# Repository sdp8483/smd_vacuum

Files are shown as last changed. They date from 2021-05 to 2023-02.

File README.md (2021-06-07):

# Manual Pick and Place SMD Vacuum

*Copy from blog post: https://samueldperry.com/2021/06/07/manual-pick-and-place-smd-vacuum/*

Until recently I used tweezers when populating surface mount parts on a PCB. Browsing around on YouTube late one night I stumbled upon a video by [SDG Electronics](https://www.youtube.com/channel/UCMiC9bSMux7i2Ds6sIqDaFg) about making a [Manual Pick and Place SMD Vacuum](https://www.youtube.com/watch?v=9G510G2gmdo&t=24s). There is also a [part 2](https://www.youtube.com/watch?v=1FnGqH_WkL4&list=RDCMUCMiC9bSMux7i2Ds6sIqDaFg&index=3) for those interested. I was then motivated to make up my own since it looked so much easier then using tweezers. There was no parts list from SDG Electronics that I could find so I set about searching for suitable components and designing my own simple controller PCB. Below is a description of the mechanical and electrical designing of the SMD Vacuum that I ended up building.

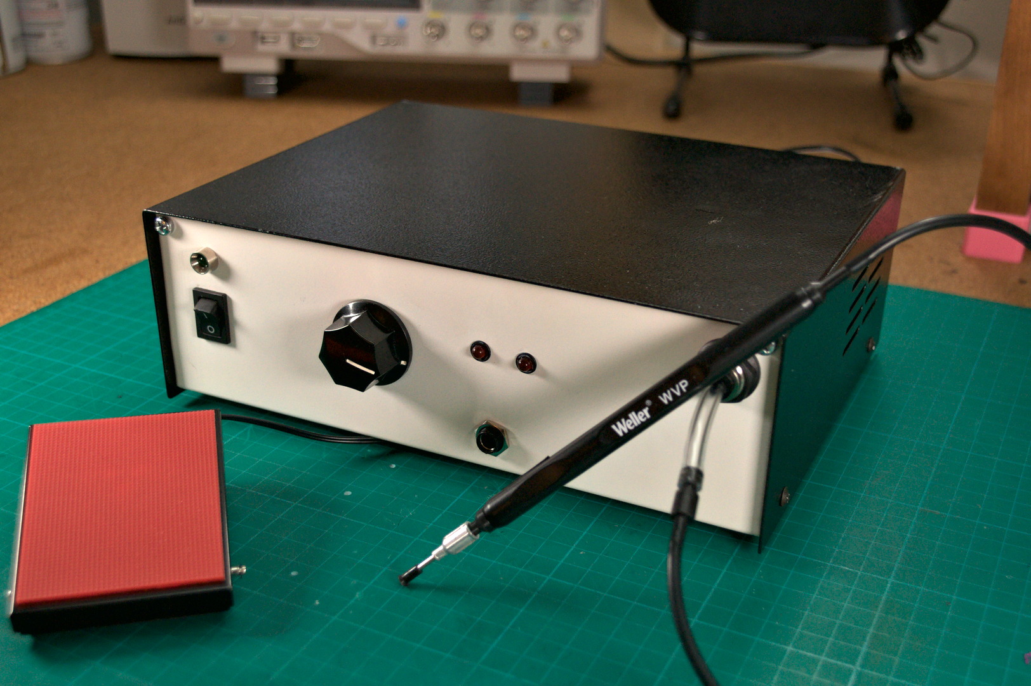
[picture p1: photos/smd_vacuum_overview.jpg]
SMD Vacuum


## Bill Of Materials

Below is a bill of materials with supplier links of all the major mechanical and electrical components. The PCB controller components are presented in a separate BOM below without suggested supplier links since all the components are generic and can be sourced from the usual suspects.
No. |Item|	Qty.|	Suggested Supplier Link
-----|----|-----|--------------------------|
1|	Metal Enclosure, 7.5″ x 9.8″ x 3.2″|	1|	[Jameco](https://www.jameco.com/webapp/wcs/stores/servlet/ProductDisplay?productId=209358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)
2|	LED Panel Mounting Hardware|	10|	[Jameco](https://www.jameco.com/webapp/wcs/stores/servlet/ProductDisplay?productId=23077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)
3|	12V Diaphragm Vacuum Pump|	1|	[eBay](https://www.ebay.com/itm/221615572829?epid=1545518177&hash=item339951475d:g:GFgAAOSwhMFZqyRF)**
4|	12V Pneumatic Shutoff Valve|	1|	[eBay](https://www.ebay.com/itm/114832826636?hash=item1abc91e10c:g:bG0AAOSwbg9gtVNb)
5|	1/4″ NPT Inline Filter/Snubber|	1|	[eBay](https://www.ebay.com/itm/132229655610)
6|	Vacuum Pick & Place Tool|	1|	[DigiKey](https://www.digikey.com/en/products/detail/apex-tool-group/T0052918499N/1801476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)
7|	1/4″ PVC Tubing|	50ft|	[McMaster-Carr](https://www.mcmaster.com/5233K52/)
8|	1/4″ Tube Fitting, Through Wall|	1|	[McMaster-Carr](https://www.mcmaster.com/5779K272/)
9|	1/4″ Tube Fitting to 1/4″ NPT Male|	3|	[McMaster-Carr](https://www.mcmaster.com/7880T125/)
10|	12V 1.3A AC to DC Power Supply|	1|	[Jameco](https://www.jameco.com/webapp/wcs/stores/servlet/ProductDisplay?productId=1919051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)
11|	1/4″ Phone Jack|	2|	[Jameco](https://www.jameco.com/webapp/wcs/stores/servlet/ProductDisplay?productId=297537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)
12|	IEC 320-C14 Power Entry Module with Fuse|	1|	[Amazon](https://www.amazon.com/Module-Socket-Connector-Blades-Holder/dp/B07TQMW2D9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)*
13|	Rocker Switch|	1|	[Amazon](https://www.amazon.com/QTEATAK-Rocker-Switch-Position-Terminals/dp/B08B84H8WL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)*
14|	3mm LED, Red/Green|	3|	[Amazon](https://www.amazon.com/Chanzon-100pcs-colors-Emitting-Assorted/dp/B01AUI4W5U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)*
15|	100k Potentiometer with Knob|	1|	[Amazon](https://www.amazon.com/TWTADE-rv24yn20s-Variable-Potentiometer-Regulation/dp/B07DHFYLRV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)*
16|	Foot Switch with 1/4″ Plug|	1|	[eBay](https://www.ebay.com/itm/272420357567)
17|	Various Fasteners and Similar Hardware|		
18|	Assembled Controller|	1|	See BOM Below

*I didn’t buy these exact items since I had them already from previous projects but these should be equivalent to what I used. Substitutions are possible for items you have on hand.

**When I was looking for a small vacuum pump eBay was flooded with the Parker 12V Dual Head Vacuum Pump which is what I got. But now it seems to be out of stock and since it looks like it was a surplus item it is probably out of stock for good. The linked vacuum pump looks like it will work just as well but I have not tested it.

No.|	Item|	Qty.
---|--------|-------
1|	PCB|	1
2|	10nF Ceramic Capacitor|	1
3|	100uF 25V Electrolytic Capacitor|	2
4|	1N4148 Diode|	2
5|	1N4007 Diode|	2
6|	IRF5305 P-channel MOSFET|	1
7|	N-channel MOSFET|	2
8|	4.7k 1/4W Through Hole Resistor|	1
9|	1k 1/4W Through Hole Resistor|	7
10|	NE555P 555 Timer|	1
11|	817 Optocoupler|	1
12|	8 pin DIP IC Socket|	1
13|	2 Position Screw Terminal|	5
14|	JST Socket with Matching Connectors and Pins|	2

## Controller PCB

Yes this project uses a 555 timer, as a electronics hobbyist I am contractually obligated to use it in at least one project. While the solution by SDG Electronics with a microcontroller is perfectly valid and what I would have normally used, I decided to finally use a 555 timer in a project. I hate the 555 timer and find it completely unnecessary in today’s microcontroller dominated world. Why use a IC that requires external components when a few lines of code and less components will produce the same result with more accurate timings? I have to admit that at the end of this project I had a little respect for the 555 timer and found it a good challenge to try to manipulate it to do what I wanted. I may briefly consider it in future simple projects.

The PCB is designed to enable milling on a CNC router such as the 3018 Pro and that is what I did. [Gerbers](https://github.com/sdp8483/smd_vacuum/tree/main/pcb/gerber) are available but be warned I did not pay any attention to the silkscreen so some component labels could be in strange spots or missing. If you want to get your PCBs made I would suggest opening the KiCAD design files and fixing the silkscreen labels before.

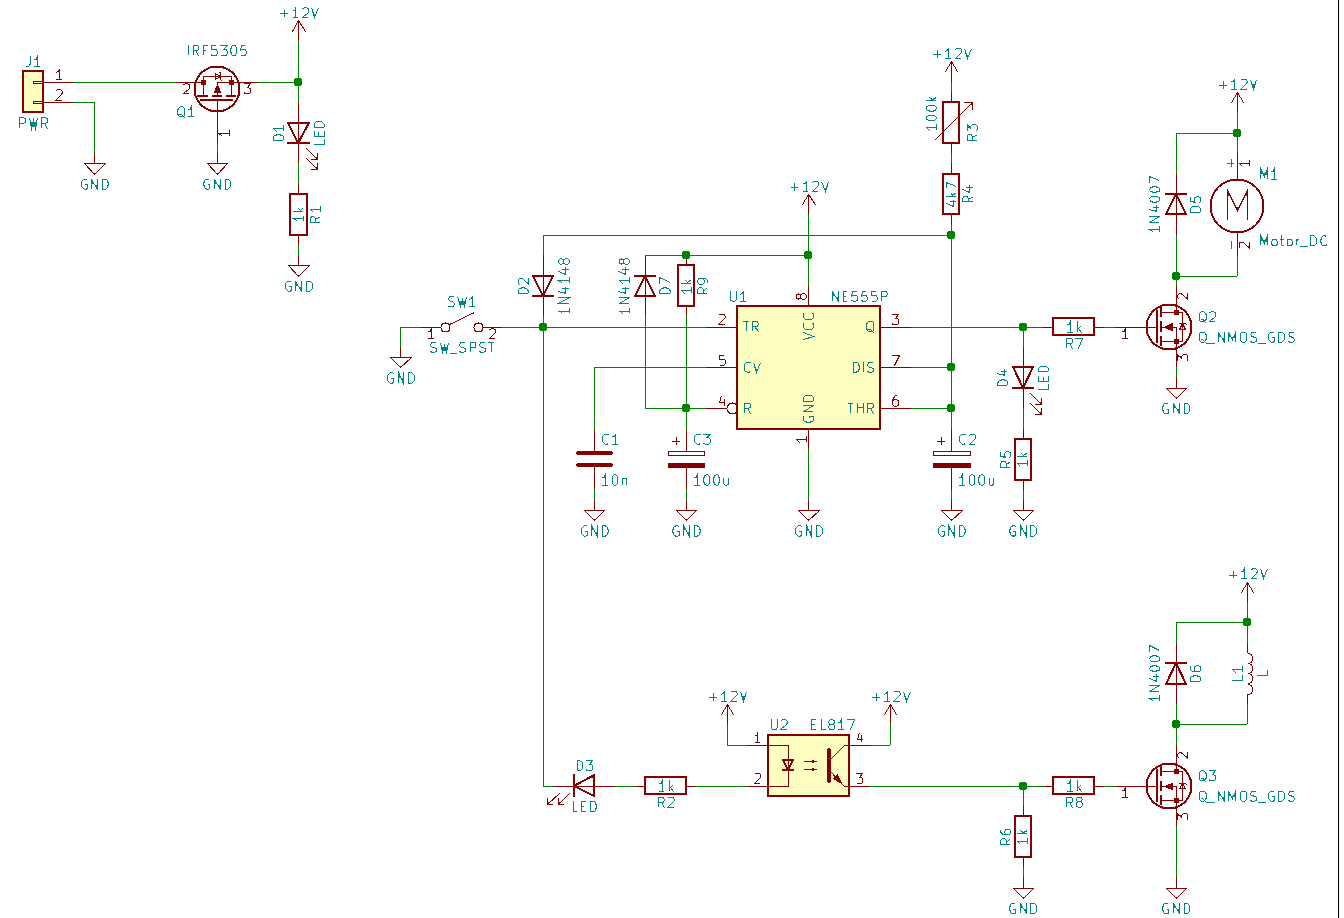
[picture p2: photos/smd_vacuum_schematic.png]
schmatic


The circuit is fairly simple, closing SW1 (the foot switch) turns on the vacuum pump and opens the shutoff valve. LED D2 and D3 will be illuminated. Releasing SW1 will close the shutoff valve turning off suction upstream of the shutoff valve and LED D3 will turn off. The vacuum pump will continue to run based on the position of the 100k potentiometer, somewhere between 1 and 15 seconds.

PCB assembly is easy when following the [interactive bom](https://github.com/sdp8483/smd_vacuum/tree/main/pcb/bom). In the pictures you may notice mine has a bodge since my first design neglected the reset on power circuitry and I had to add that after I noticed that sometimes on first power up the controller would turn on the vacuum pump. The PCB design has been updated with those components so no need for you to bodge them in.

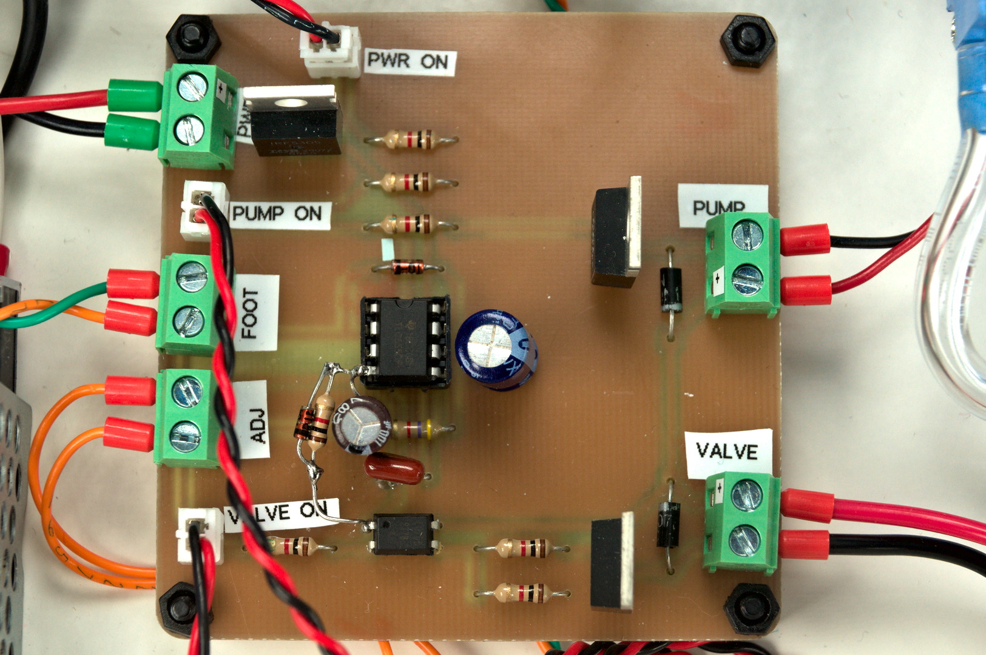
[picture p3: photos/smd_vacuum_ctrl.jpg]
PCB


## Assembly

I will go over briefly how I assembled my SMD Vacuum but will omit many details since you most likely will not be using the same vacuum pump and you may wish your layout to be slightly different.

First thing I did was to arrange all the components inside the enclosure so that I could see if everything would fit. I roughly knew that I wanted to keep the power supply and its AC wiring on the left of the case, with the controller in the middle and the pneumatics on the right side of the case. I also arranged the front and back panels to look like I wanted. Pencil works great since it can easily be cleaned off later.

I started with mounting the AC power input socket, rocker switch, and 12V power supply. I wired the rocker switch to cut power to the input of the 12V power supply so that when the unit is turned off there will be zero current draw. Don’t forget to attach the earth ground from the AC socket to the case using a bolt and star washer. Sand off some of the paint under the washer on the case to make a good metal to metal connection. Also attach the earth ground of the 12V power supply to this same point. This way the case is grounded and is safer.

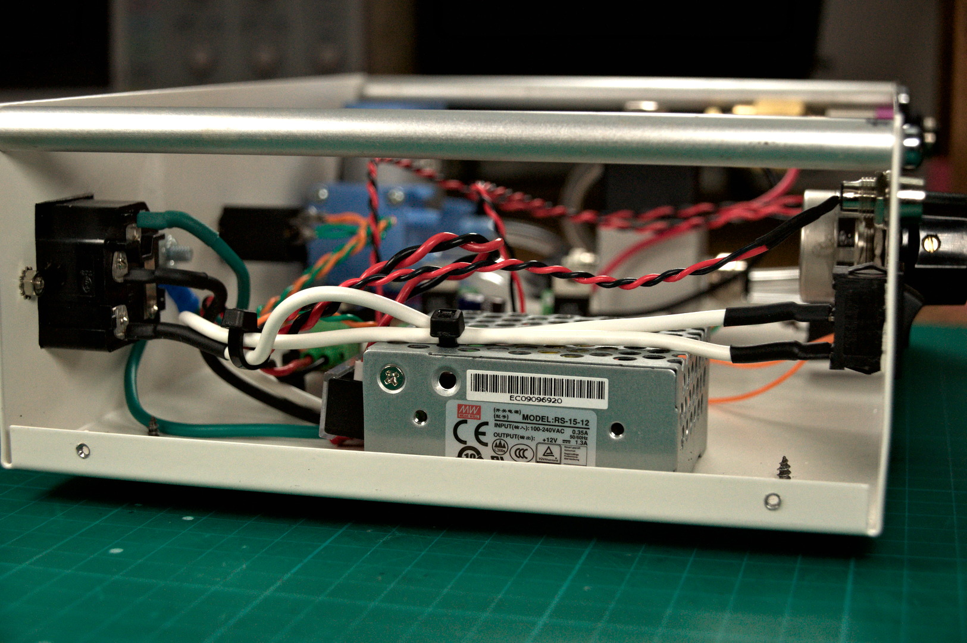
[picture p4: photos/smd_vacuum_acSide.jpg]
AC Power Side

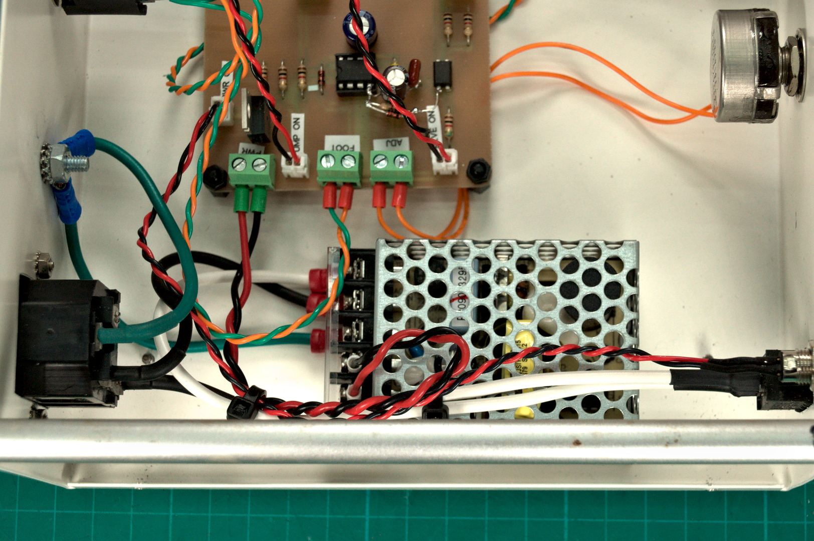
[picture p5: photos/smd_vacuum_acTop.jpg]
AC Power Top

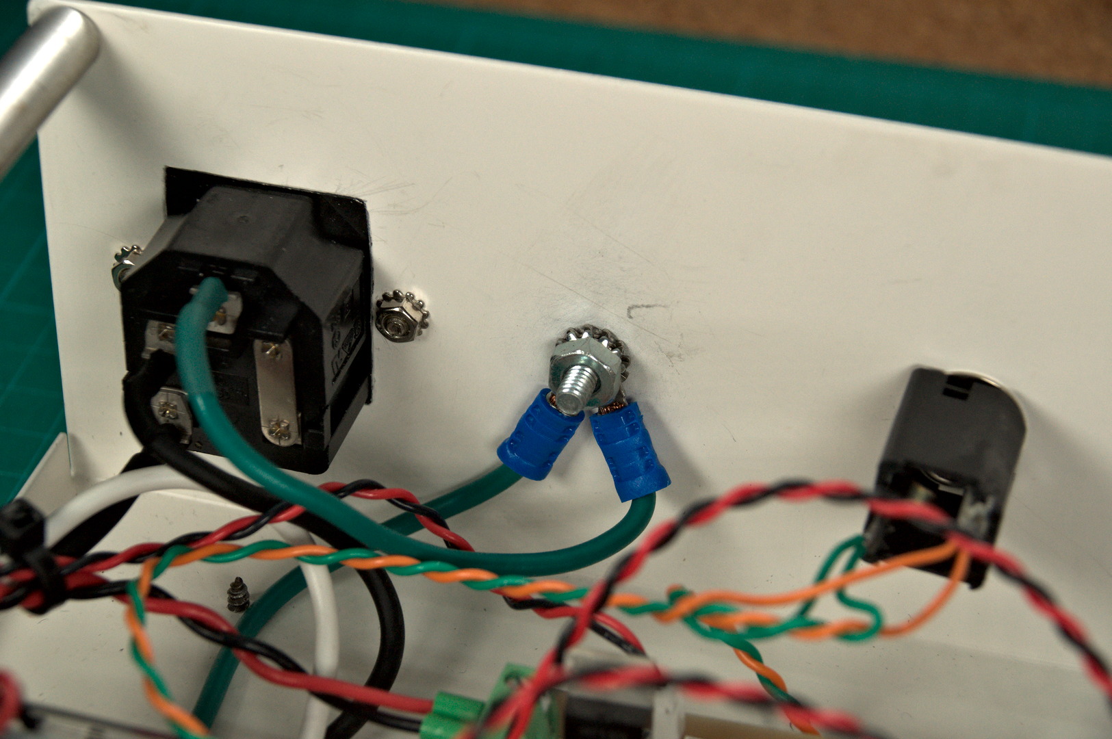
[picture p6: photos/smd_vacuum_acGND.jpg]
AC Power GND


I then mounted the controller PCB using nylon standoffs near the center of the case and oriented it so that the power input terminal is close to the 12V power supply. At the same time I mounted the 100k potentiometer, LEDs, and 1/4″ jacks. I used two 1/4″ jacks in parallel because I wanted both the front and back panels to have a jack. This way I can plug the foot switch into whatever panel is most convenient for wire management.

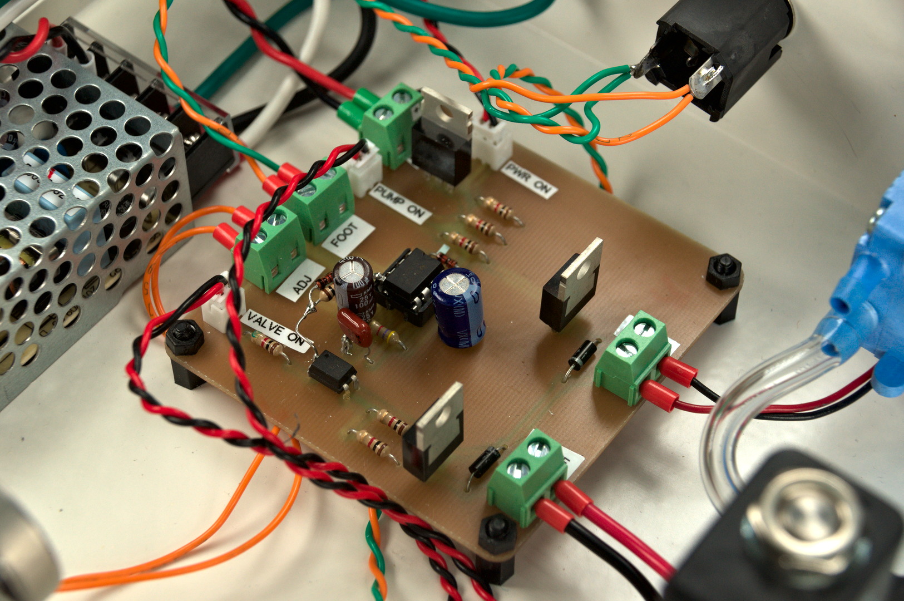
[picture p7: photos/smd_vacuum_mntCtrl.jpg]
Controler Mount

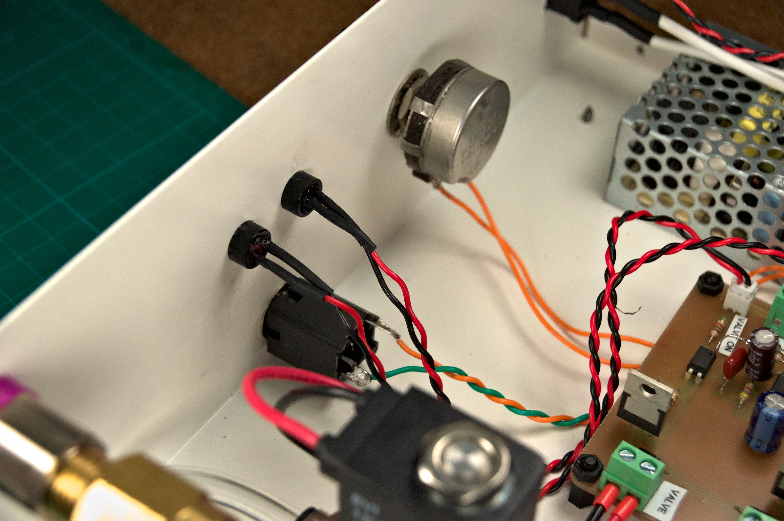
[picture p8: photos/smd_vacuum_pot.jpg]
Pot and LEDs


For the pnumatics I 3D printed some standoffs so that they would not be resting directly on the case. This was mostly done because of the length of fasteners I had and also to dampen the noise produced by the vacuum pump. I plumbed the punmatics as shown below with the shutoff valve between the pump and the filter followed by the panel mounted 1/4″ tube fitting. The filter is absolutely necessary as I have already sucked up quite a few 0603 parts and having the filter saves the shutoff valve and pump from damage.

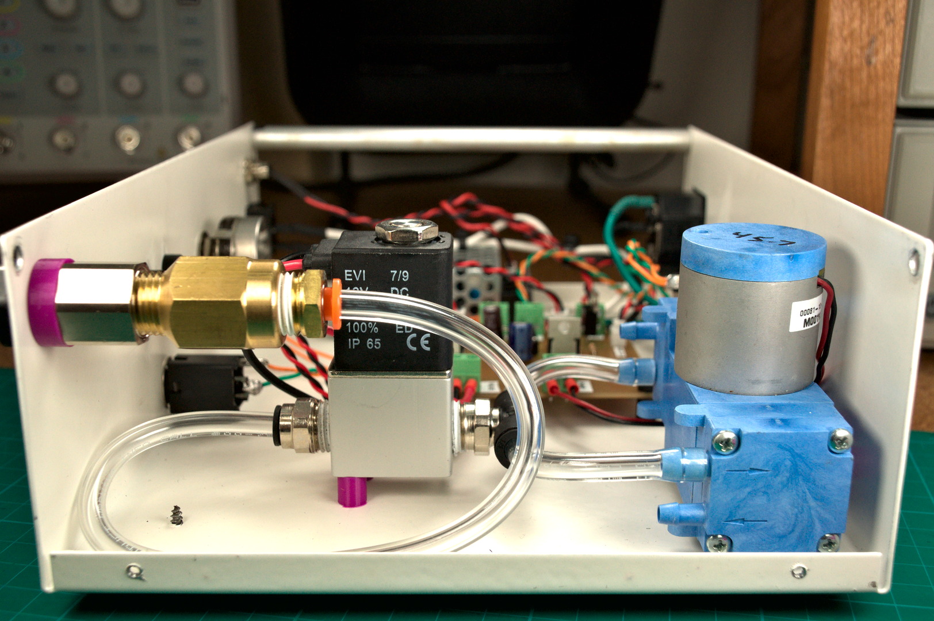
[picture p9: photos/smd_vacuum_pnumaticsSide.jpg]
pnumatics side

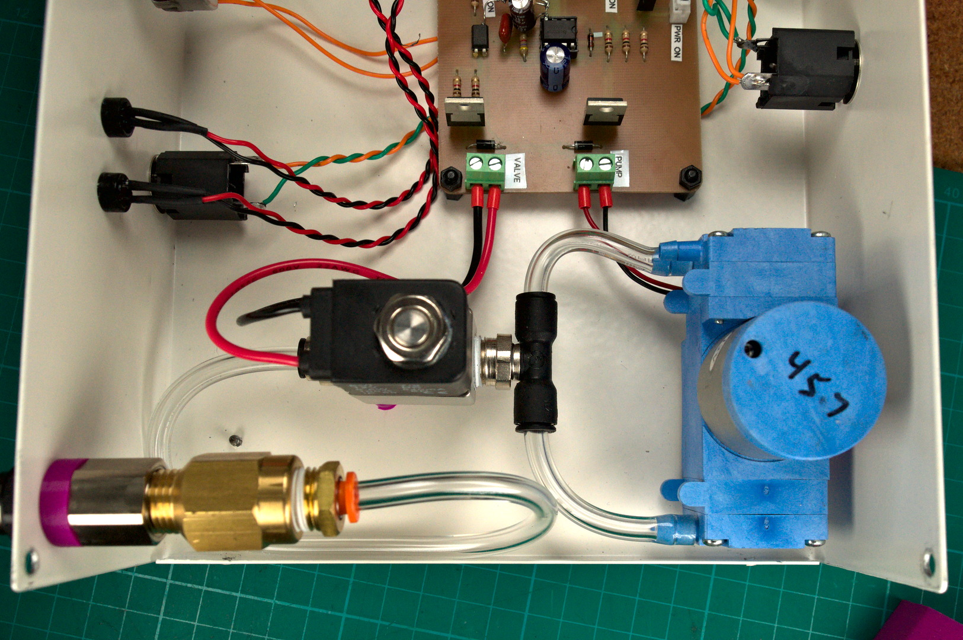
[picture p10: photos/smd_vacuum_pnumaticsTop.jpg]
pnumatics top


That was about all the steps I took for assembly, fairly simple. The aluminum bars in the pictures were added to increase the stiffness of the front and back panel when plugging in connectors and tubing.

## Hand piece

Aside from the vacuum pump the second most important item for this build is the hand piece. This is the part that you hold and use to pickup SMD parts. I was able to find a used Weller WVP on eBay. I would suggest looking there or other used market places first since it is relatively expensive brand new for some reason. The part number to search for is T0052918499N or look for replacement parts for a Weller WR3M Station. [DigiKey](https://github.com/sdp8483/smd_vacuum/tree/main/pcb/bom) sells a new Weller WVP for $88. The Weller WVP is adapted to the SMD Vacuum by cutting a small section of the 1/4″ PVC tubing and inserting the plastic nozzle on the end hand piece into the tubing as shown below. Finally block the hole on the side of the Weller WVP since we are using to foot pedal to control suction and not your finger.

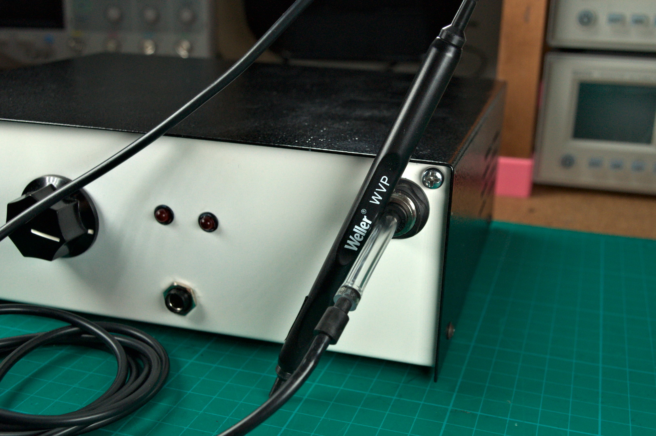
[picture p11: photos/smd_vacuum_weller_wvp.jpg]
Weller WVP


This hand piece feels really nice and works well for me. Having said that if you cannot find one for a decent price or feel like making your own hand piece I did do a little experimentation and found that it is possible to make something similar while not as well polished. I used a [1/8″ OD Brass Tube](https://www.mcmaster.com/8859K19/) and connected it to the front port of the SMD Vacuum using [1/4″ OD Soft Tygon PVC Tubing](https://www.mcmaster.com/5552k23/). The clear PVC tubing used inside the SMD Vacuum is a little stiff for my liking and I found that Tygon tubing is slightly more pliant. The photos below show the rough setup I was experimenting with before I found the Weller Hand Piece. My plan was to 3D print a case to go around the brass tube for gripping and to also 3D print adapters so that the nozzles could connect better to the brass tube. As pictured it works fine although not very ergonomic. For nozzles I used a rubber protective cover that comes on the engraving bits for the 3018 pro with a small hole that I drilled in the end. This setup was a rough prototype that I would have refined more had I not picked up a Weller WVP.

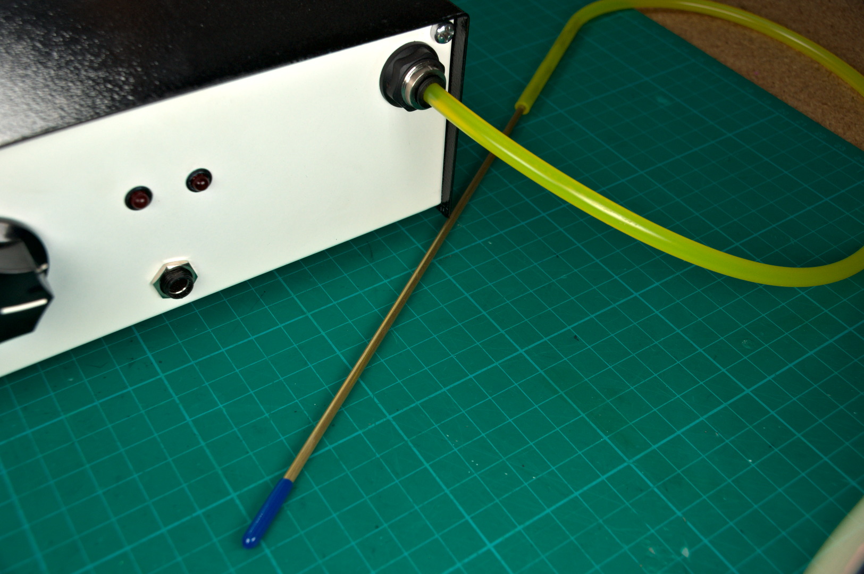
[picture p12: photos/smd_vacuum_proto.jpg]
proto hand piece


## Nozzles

Nozzles, you will need some. The Weller WVP comes with some nozzles and suction cup tips. You can also get these nozzle and cups with one of the cheap [vacuum suction pens](https://www.amazon.com/Jiayouy-Precision-Component-Placement-Interchangeable/dp/B08SWG12G3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). These nozzles and suction cups are great for picking up larger SMD packages like microcontrollers and power MOSFETs but they are not useful for small packages such as 0603 resistors and capacitors. The suction cup gets in the way and grips the part so well that it will not release when suction is turned off. Removing the suction cup is not possible since the nozzle ID is large enough that a 0603 resistor can get sucked up it. Remember that filter, this is why it is installed before the shutoff valve.

What I found that works great for these small packages is [blunt tip needles for syringes](https://www.amazon.com/dp/B07RSTQ6RV?psc=1&ref=ppx_yo2_dt_b_product_details). I got a variety pack with 14ga, 16ga,18ga, 20ga, 22ga and 25ga needles along with some syringes. I found the 20ga needle (pink) to be the perfect size for picking up 0603 packages along with SOT-23 transistors and some larger packages. The part drops off as soon a suction is off and you can see the part while manipulating it. The only problem is that the nozzle requires you to work with the hand piece vertical since it does not have the angle on it like the nozzles that came with the Weller WVP. If I get adventurous I may try bending one someday but for now I found working vertical gave me better position control.

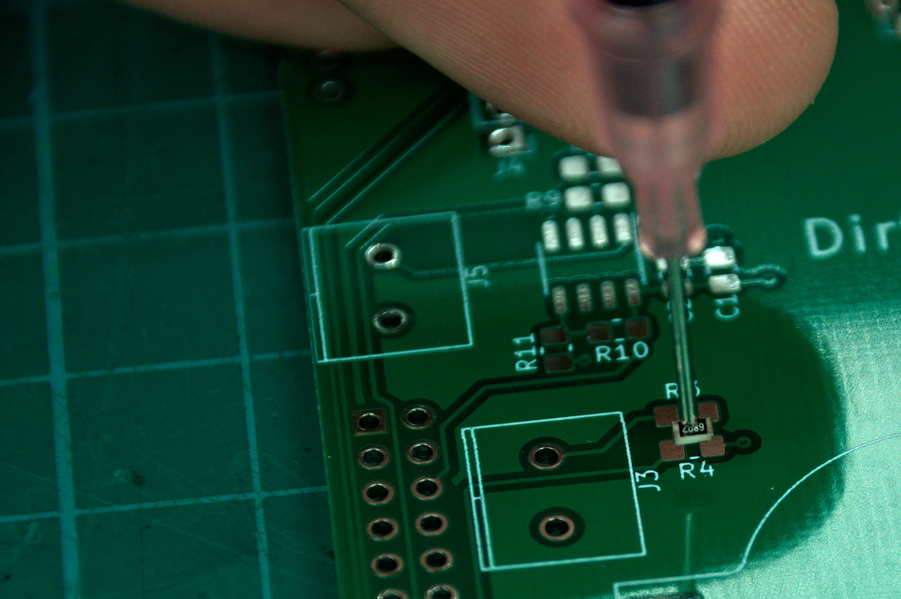
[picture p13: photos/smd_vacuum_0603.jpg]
nozzle in use 1

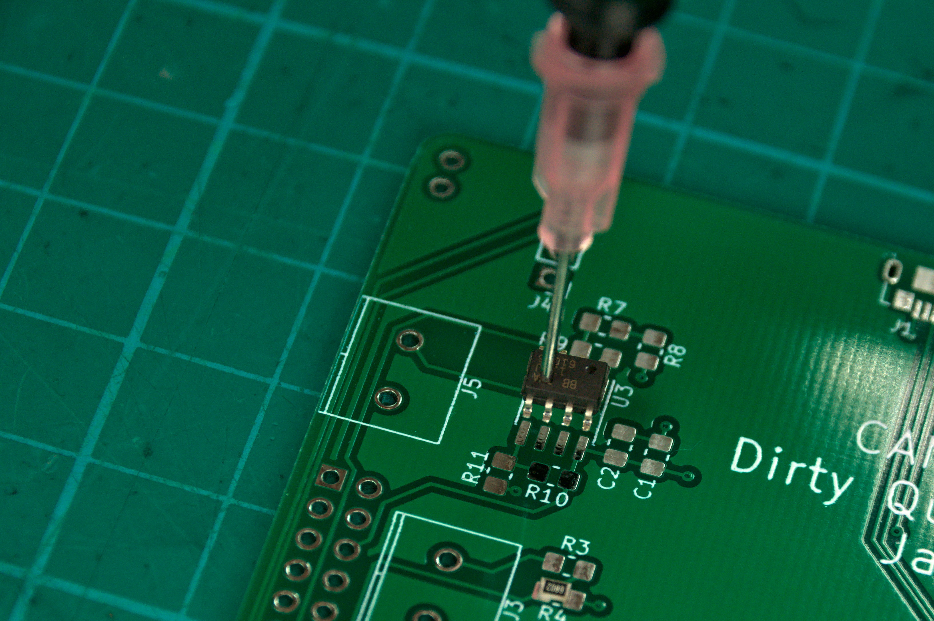
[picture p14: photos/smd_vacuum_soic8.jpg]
nozzle in use 2


## Conclusion

That wraps up this project. I am very happy with how it turned out and its function. I successfully assembled a small run of 10 PCBs with 64 components per board using this SMD Vacuum without any issues. Utilizing the blunt needle tip along with one of the suction cup tips that came with the Weller WVP I was able to handle all the SMD parts for those PCBs. The smallest package size was 0603 and the largest package was a ESP-12F WiFi module. The SMD Vacuum had enough suction power to lift everything and made placement easy. Goodby tweezers, hello SMD Vacuum.

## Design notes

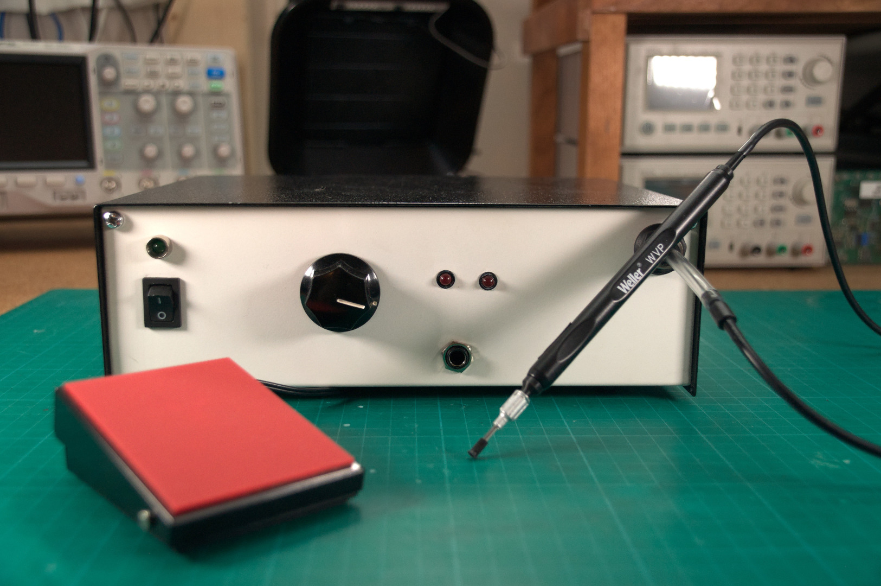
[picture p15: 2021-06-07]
photos/smd_vacuum_cover.jpg

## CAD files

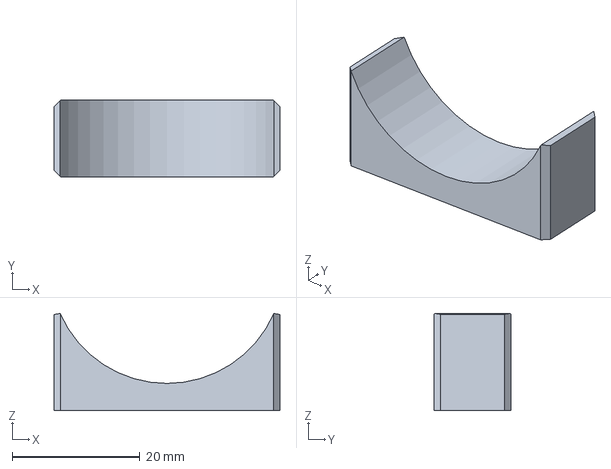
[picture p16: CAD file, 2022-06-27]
enclosure/KarlssonRobotics_pump_mount-base.amf
35.4 x 12.0 x 15.2 mm

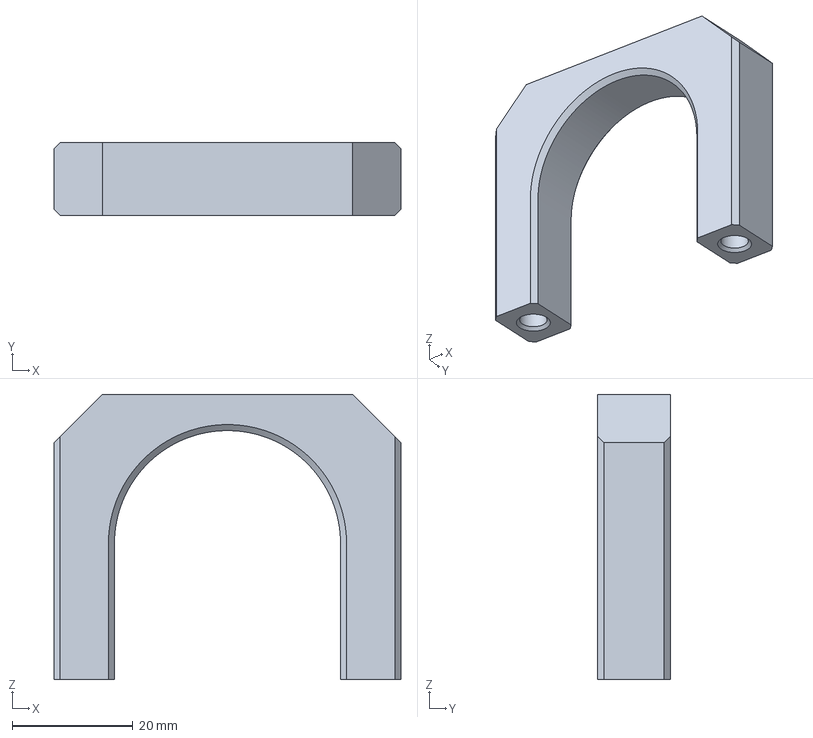
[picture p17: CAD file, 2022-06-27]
enclosure/KarlssonRobotics_pump_mount-clamp.amf
57.4 x 12.0 x 47.2 mm

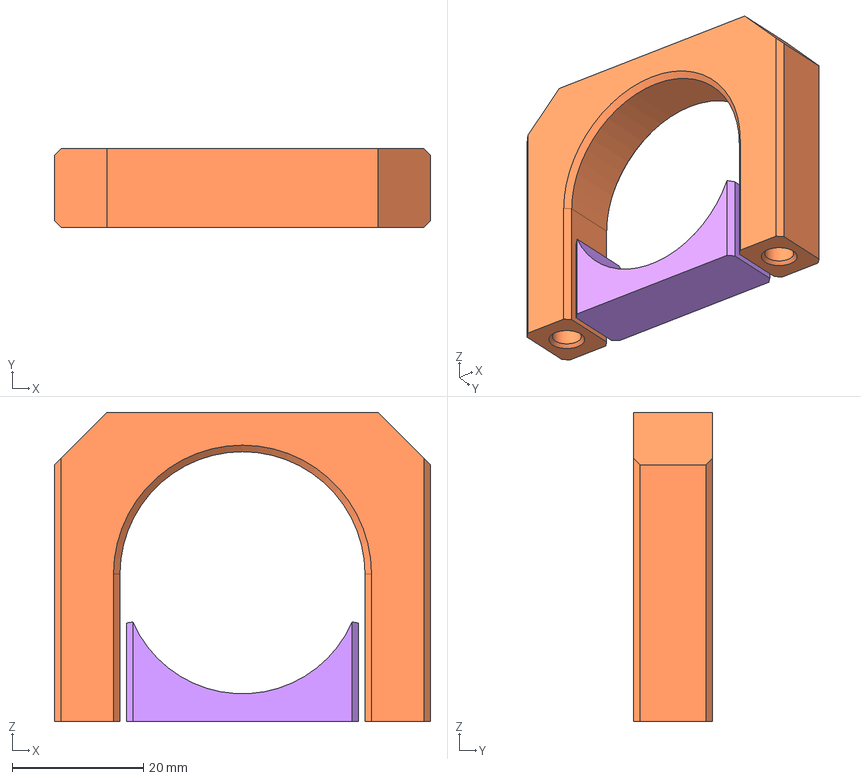
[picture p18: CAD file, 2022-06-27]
enclosure/KarlssonRobotics_pump_mount.FCStd
57.4 x 12.0 x 47.2 mm
clamp
base

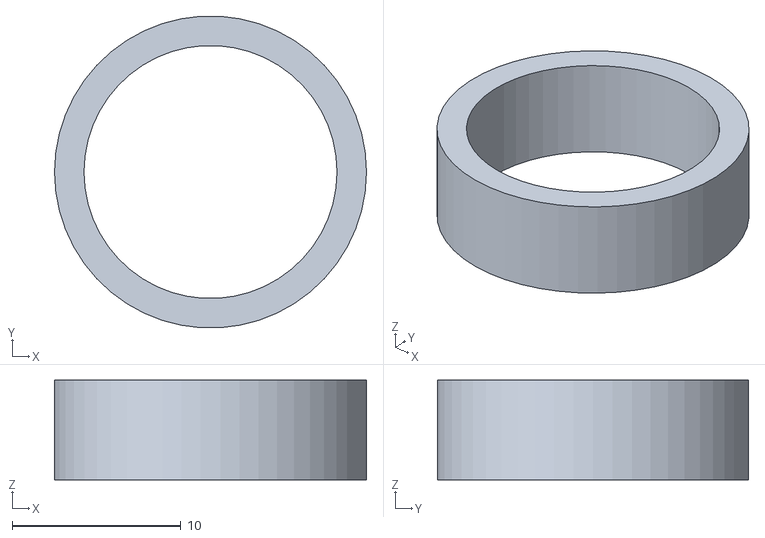
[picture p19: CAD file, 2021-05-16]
enclosure/air_spacer.stl
18.5 x 18.5 x 5.90

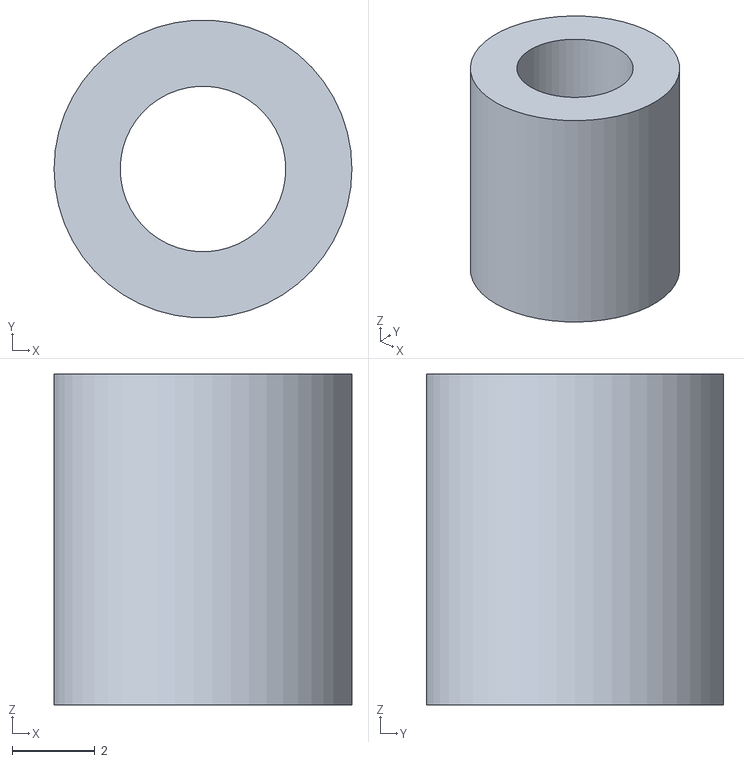
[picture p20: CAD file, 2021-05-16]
enclosure/valve_spacer.stl
7.20 x 7.19 x 8.00

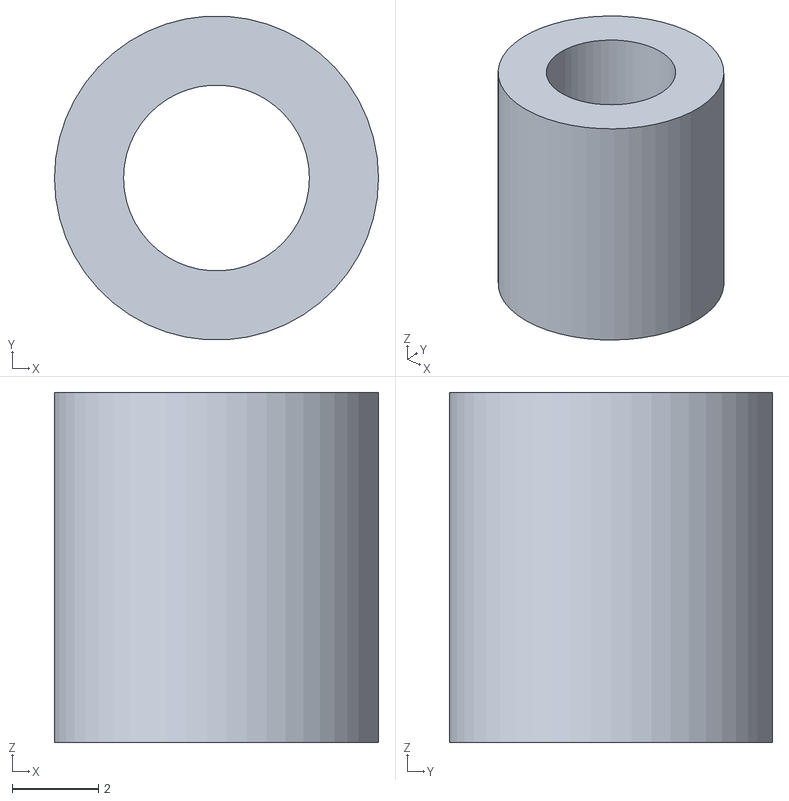
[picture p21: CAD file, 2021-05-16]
enclosure/pump_spacer.stl
7.50 x 7.49 x 8.10

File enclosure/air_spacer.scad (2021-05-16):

$fn = 50;

L = 5.9;
id = 15;
od = 18.5;

difference() {
    cylinder(h=L, d=od);
    cylinder(h=L, d=id);
}

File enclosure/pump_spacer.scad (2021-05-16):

$fn = 50;

L = 12.3-3-1.2;
id = 4.3;
od = 2*((id/2) + (0.4*4));

difference() {
    cylinder(h=L, d=od);
    cylinder(h=L, d=id);
}

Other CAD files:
enclosure/valve_spacer.scad

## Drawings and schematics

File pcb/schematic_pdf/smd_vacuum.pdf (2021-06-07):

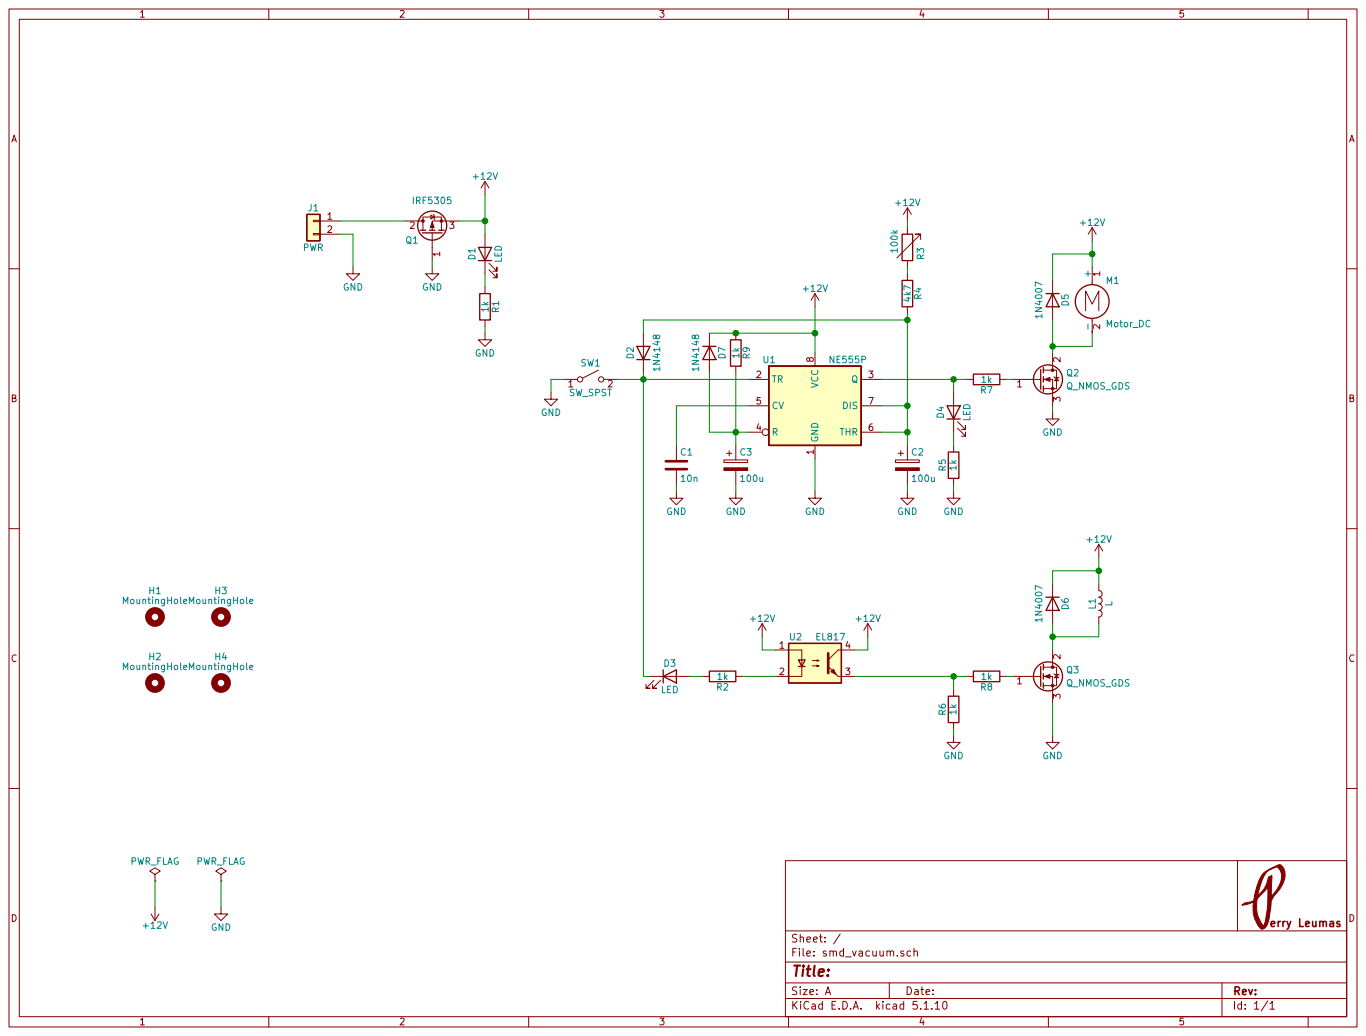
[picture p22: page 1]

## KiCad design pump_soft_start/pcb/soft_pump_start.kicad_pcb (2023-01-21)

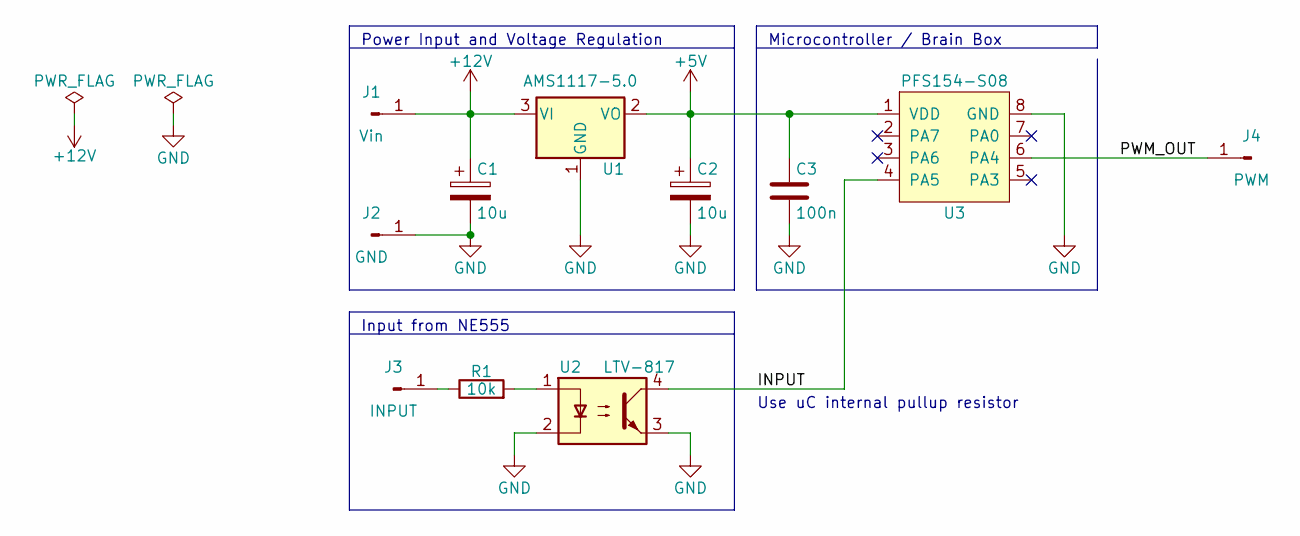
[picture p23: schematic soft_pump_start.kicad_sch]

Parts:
C1, C2: 10u; CP_Radial_D5.0mm_P2.50mm
C3: 100n; C_0603_1608Metric_Pad1.08x0.95mm_HandSolder
J1: Vin; SolderWire-0.5sqmm_1x01_D0.9mm_OD2.1mm
J2: GND; SolderWire-0.5sqmm_1x01_D0.9mm_OD2.1mm
J3: INPUT; SolderWire-0.5sqmm_1x01_D0.9mm_OD2.1mm
J4: PWM; SolderWire-0.5sqmm_1x01_D0.9mm_OD2.1mm
R1: 10k; R_0603_1608Metric_Pad0.98x0.95mm_HandSolder
U1: AMS1117-5.0; SOT-223-3_TabPin2
U2: LTV-817; DIP-4_W7.62mm
U3: PFS154-S08; SOP-8_3.9x4.9mm_P1.27mm

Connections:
+5V: C2.1, C3.1, U1.2 (VO), U3.1 (VDD)
+12V: C1.1, J1.1, U1.3 (VI)
/INPUT: U2.4, U3.4 (PA5)
/PWM_OUT: J4.1, U3.6 (PA4)
GND: C1.2, C2.2, C3.2, J2.1, U1.1 (GND), U2.2, U2.3, U3.8 (GND)
unnamed: J3.1, R1.1
unnamed: R1.2, U2.1

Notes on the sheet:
Microcontroller / Brain Box
Input from NE555
Use uC internal pullup resistor
Power Input and Voltage Regulation

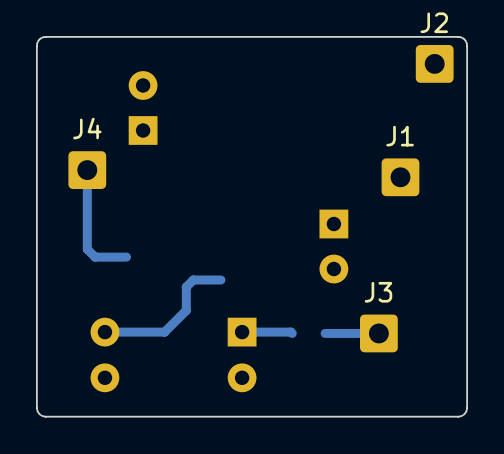
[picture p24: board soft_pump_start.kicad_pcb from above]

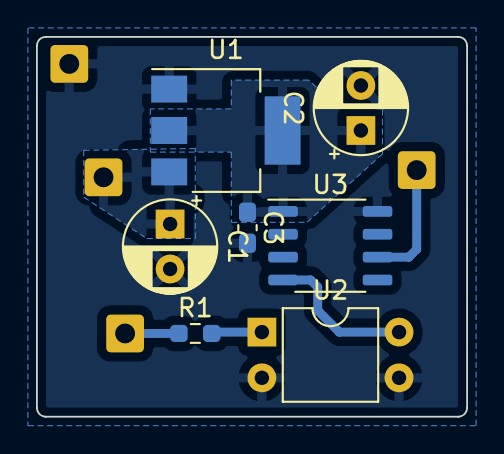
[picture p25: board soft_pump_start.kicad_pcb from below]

Board: 2 copper layers, 23.9 x 21.1 mm, 11 parts (7 on the bottom side), 7 nets.

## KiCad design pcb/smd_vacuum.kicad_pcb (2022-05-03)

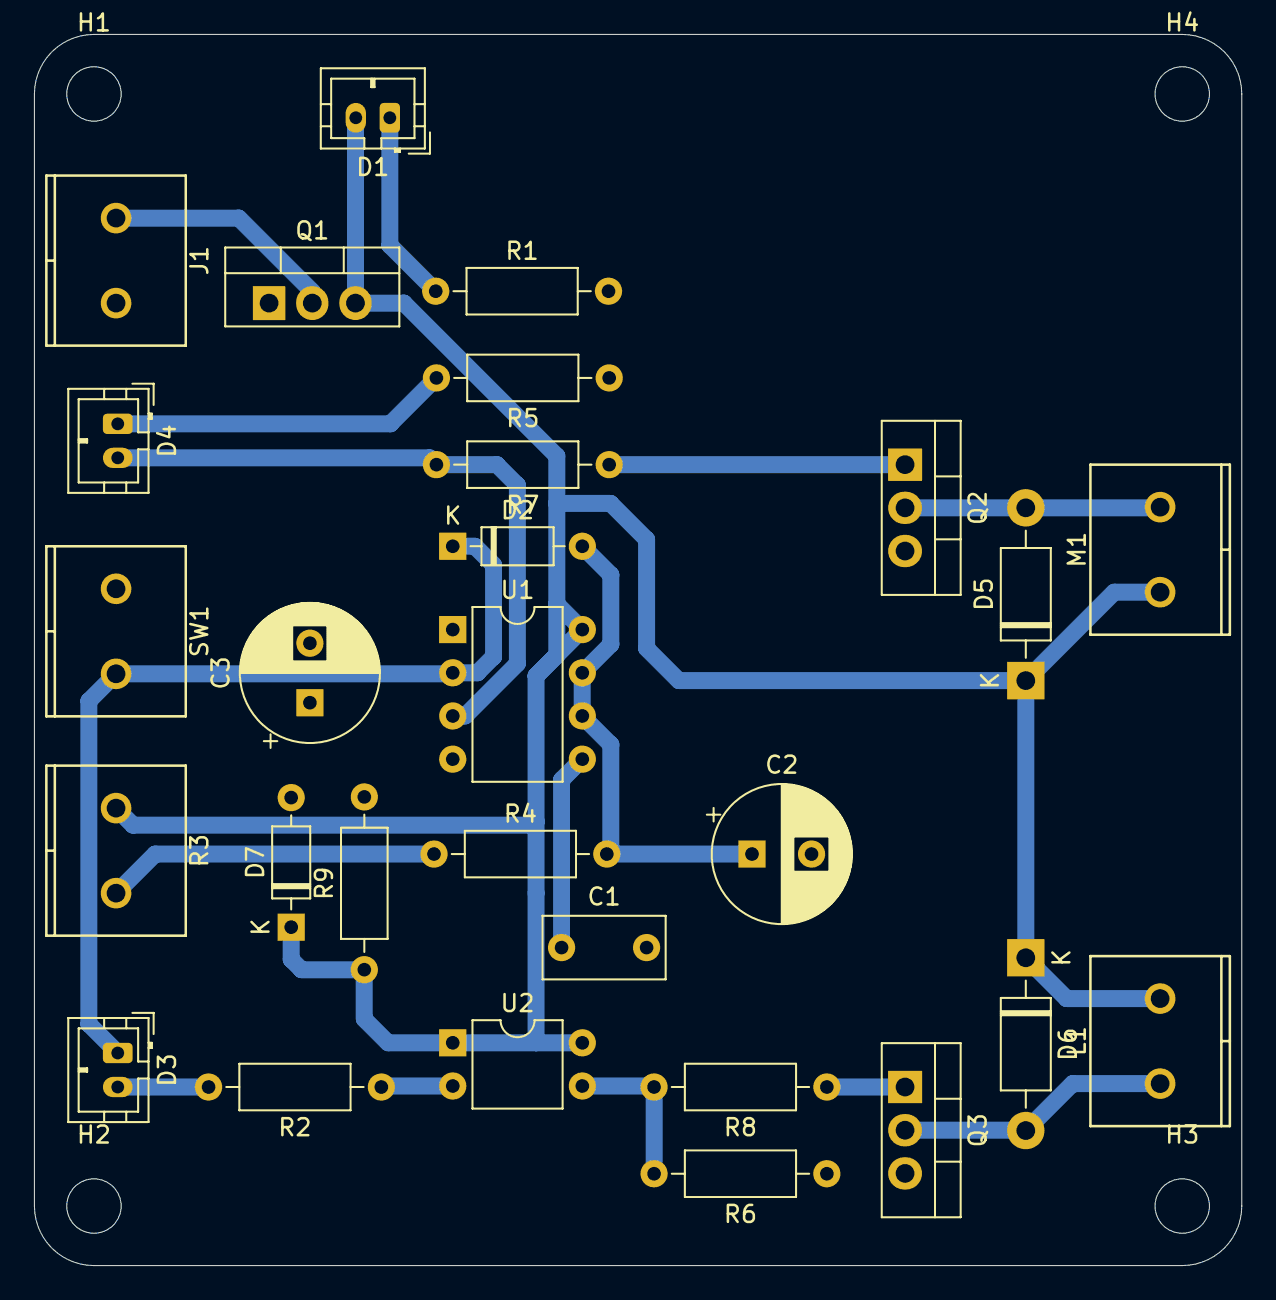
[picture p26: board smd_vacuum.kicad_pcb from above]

Board: 2 copper layers, 71.0 x 72.4 mm, 32 parts (0 on the bottom side), 18 nets.

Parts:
C1: 10n; C_Rect_L7.0mm_W3.5mm_P5.00mm
C2, C3: 100u; CP_Radial_D8.0mm_P3.50mm
D1, D3, D4: LED; JST_PH_B2B-PH-K_1x02_P2.00mm_Vertical
D2, D7: 1N4148; D_DO-35_SOD27_P7.62mm_Horizontal
D5, D6: 1N4007; D_DO-41_SOD81_P10.16mm_Horizontal
H1, H2, H3, H4: MountingHole; MountingHole_3.2mm_M3
J1: PWR; WJ127-5.0-2P
L1: L; WJ127-5.0-2P
M1: Motor_DC; WJ127-5.0-2P
Q1: IRF5305; TO-220-3_Vertical
Q2, Q3: Q_NMOS_GDS; TO-220-3_Vertical
R1, R2, R5, R6, R7, R8, R9: 1k; R_Axial_DIN0207_L6.3mm_D2.5mm_P10.16mm_Horizontal
R3: 100k; WJ127-5.0-2P
R4: 4k7; R_Axial_DIN0207_L6.3mm_D2.5mm_P10.16mm_Horizontal
SW1: SW_SPST; WJ127-5.0-2P
U1: NE555P; DIP-8_W7.62mm
U2: EL817; DIP-4_W7.62mm

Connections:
+12V: D1.2, D5.1, D6.1, D7.1, L1.2, M1.1, Q1.3, R3.1, R9.1, U1.8, U2.1, U2.4
GND: C1.2, C2.2, C3.2, J1.2, Q1.1, Q2.3, Q3.3, R1.2, R5.1, R6.1, SW1.1, U1.1
unnamed: C1.1, U1.5
unnamed: C2.1, D2.2, R4.2, U1.6, U1.7
unnamed: C3.1, D7.2, R9.2, U1.4
unnamed: D1.1, R1.1
unnamed: D2.1, D3.1, SW1.2, U1.2
unnamed: D3.2, R2.2
unnamed: D4.1, R5.2
unnamed: D4.2, R7.2, U1.3
unnamed: D5.2, M1.2, Q2.2
unnamed: D6.2, L1.1, Q3.2
unnamed: J1.1, Q1.2
unnamed: Q2.1, R7.1
unnamed: Q3.1, R8.1
unnamed: R2.1, U2.2
unnamed: R3.2, R4.1
unnamed: R6.2, R8.2, U2.3

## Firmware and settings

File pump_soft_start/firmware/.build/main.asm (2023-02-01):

;--------------------------------------------------------
; File Created by SDCC : free open source ANSI-C Compiler
; Version 4.2.0 #13081 (Linux)
;--------------------------------------------------------
	.module main
	.optsdcc -mpdk14
	

; default segment ordering in RAM for linker
	.area DATA
	.area OSEG (OVR,DATA)

;--------------------------------------------------------
; Public variables in this module
;--------------------------------------------------------
	.globl __sdcc_external_startup
	.globl _main
	.globl __delay_loop_32
	.globl __delay_loop_16
	.globl __delay_loop_8
	.globl __misclvr
	.globl __misc2
	.globl __misc
	.globl __pwmg2cubl
	.globl __pwmg2cubh
	.globl __pwmg2dtl
	.globl __pwmg2dth
	.globl __pwmg2s
	.globl __pwmg2c
	.globl __pwmg1cubl
	.globl __pwmg1cubh
	.globl __pwmg1dtl
	.globl __pwmg1dth
	.globl __pwmg1s
	.globl __pwmg1c
	.globl __pwmg0cubl
	.globl __pwmg0cubh
	.globl __pwmg0dtl
	.globl __pwmg0dth
	.globl __pwmg0s
	.globl __pwmg0c
	.globl __gpcs
	.globl __gpcc
	.globl __bgtr
	.globl __tm3b
	.globl __tm3s
	.globl __tm3ct
	.globl __tm3c
	.globl __tm2b
	.globl __tm2s
	.globl __tm2ct
	.globl __tm2c
	.globl __t16c
	.globl __t16m
	.globl __pbph
	.globl __pbc
	.globl __pb
	.globl __pbdier
	.globl __paph
	.globl __pac
	.globl __pa
	.globl __padier
	.globl __integs
	.globl __intrq
	.globl __inten
	.globl __eoscr
	.globl __ilrcr
	.globl __ihrcr
	.globl __clkmd
	.globl __sp
	.globl __flag
	.globl __delay_loop_32_PARM_1
	.globl __delay_loop_16_PARM_1
	.globl __delay_loop_8_PARM_1
;--------------------------------------------------------
; special function registers
;--------------------------------------------------------
	.area RSEG (ABS)
	.org 0x0000
__flag	=	0x0000
__sp	=	0x0002
__clkmd	=	0x0003
__ihrcr	=	0x000b
__ilrcr	=	0x0039
__eoscr	=	0x000a
__inten	=	0x0004
__intrq	=	0x0005
__integs	=	0x000c
__padier	=	0x000d
__pa	=	0x0010
__pac	=	0x0011
__paph	=	0x0012
__pbdier	=	0x000e
__pb	=	0x0014
__pbc	=	0x0015
__pbph	=	0x0016
__t16m	=	0x0006
__t16c::
	.ds 2
__tm2c	=	0x001c
__tm2ct	=	0x001d
__tm2s	=	0x0017
__tm2b	=	0x0009
__tm3c	=	0x0032
__tm3ct	=	0x0033
__tm3s	=	0x0034
__tm3b	=	0x0035
__bgtr	=	0x001a
__gpcc	=	0x0018
__gpcs	=	0x0019
__pwmg0c	=	0x0020
__pwmg0s	=	0x0021
__pwmg0dth	=	0x0022
__pwmg0dtl	=	0x0023
__pwmg0cubh	=	0x0024
__pwmg0cubl	=	0x0025
__pwmg1c	=	0x0026
__pwmg1s	=	0x0027
__pwmg1dth	=	0x0028
__pwmg1dtl	=	0x0029
__pwmg1cubh	=	0x002a
__pwmg1cubl	=	0x002b
__pwmg2c	=	0x002c
__pwmg2s	=	0x002d
__pwmg2dth	=	0x002e
__pwmg2dtl	=	0x002f
__pwmg2cubh	=	0x0030
__pwmg2cubl	=	0x0031
__misc	=	0x0008
__misc2	=	0x000f
__misclvr	=	0x001b
;--------------------------------------------------------
; ram data
;--------------------------------------------------------
	.area DATA
__delay_loop_8_PARM_1:
	.ds 1
__delay_loop_16_PARM_1:
	.ds 2
__delay_loop_32_PARM_1:
	.ds 4
_main_sloc0_1_0:
	.ds 2
;--------------------------------------------------------
; overlayable items in ram
;--------------------------------------------------------
;--------------------------------------------------------
; Stack segment in internal ram
;--------------------------------------------------------
	.area	SSEG
__start__stack:
	.ds	1

;--------------------------------------------------------
; absolute external ram data
;--------------------------------------------------------
	.area DABS (ABS)
;--------------------------------------------------------
; interrupt vector
;--------------------------------------------------------
	.area HOME
__interrupt_vect:
	.area	HEADER (ABS)
	.org	 0x0020
	reti
;--------------------------------------------------------
; global & static initialisations
;--------------------------------------------------------
	.area HOME
	.area GSINIT
	.area GSFINAL
	.area GSINIT
	.area	PREG (ABS)
	.org 0x00
p::
	.ds 2
	.area	HEADER (ABS)
	.org 0x0000
	nop
	clear	p+1
	mov	a, #s_OSEG
	add	a, #l_OSEG + 1
	and	a, #0xfe
	mov.io	sp, a
	call	__sdcc_external_startup
	goto	s_GSINIT
	.area GSINIT
__sdcc_init_data:
	mov	a, #s_DATA
	mov	p, a
	goto	00002$
00001$:
	mov	a, #0x00
	idxm	p, a
	inc	p
	mov	a, #s_DATA
00002$:
	add	a, #l_DATA
	ceqsn	a, p
	goto	00001$
	.area GSFINAL
	goto	__sdcc_program_startup
;--------------------------------------------------------
; Home
;--------------------------------------------------------
	.area HOME
	.area HOME
__sdcc_program_startup:
	goto	_main
;	return from main will return to caller
;--------------------------------------------------------
; code
;--------------------------------------------------------
	.area CODE
;	delay.h: 34: void _delay_loop_8(uint8_t loop_ctr) {
;	-----------------------------------------
;	 function _delay_loop_8
;	-----------------------------------------
__delay_loop_8:
;	delay.h: 44: __endasm;
	00001$:
; 4 cycles per loop
	dzsn	__delay_loop_8_PARM_1 ; 1 cycle + 1 cycle for final skip
	goto	00001$ ; 2 cycles
00101$:
;	delay.h: 45: }
	ret
;	delay.h: 48: void _delay_loop_16(uint16_t loop_ctr) {
;	-----------------------------------------
;	 function _delay_loop_16
;	-----------------------------------------
__delay_loop_16:
;	delay.h: 65: __endasm;
	00001$:
; 8 cycles per loop
	nop	; 1 cycle
	dec	__delay_loop_16_PARM_1+0 ; 1 cycle
	subc	__delay_loop_16_PARM_1+1 ; 1 cycle
	mov	a, __delay_loop_16_PARM_1+0 ; 1 cycle
	or	a, __delay_loop_16_PARM_1+1 ; 1 cycle
	t1sn	f, z ; 1 cycle + 1 cycle for final skip
	goto	00001$ ; 2 cycles
00101$:
;	delay.h: 66: }
	ret
;	delay.h: 69: void _delay_loop_32(uint32_t loop_ctr) {
;	-----------------------------------------
;	 function _delay_loop_32
;	-----------------------------------------
__delay_loop_32:
;	delay.h: 94: __endasm;
	00001$:
; 12 cycles per loop
	nop	; 1 cycle
	dec	__delay_loop_32_PARM_1+0 ; 1 cycle
	subc	__delay_loop_32_PARM_1+1 ; 1 cycle
	subc	__delay_loop_32_PARM_1+2 ; 1 cycle
	subc	__delay_loop_32_PARM_1+3 ; 1 cycle
	mov	a, __delay_loop_32_PARM_1+0 ; 1 cycle
	or	a, __delay_loop_32_PARM_1+1 ; 1 cycle
	or	a, __delay_loop_32_PARM_1+2 ; 1 cycle
	or	a, __delay_loop_32_PARM_1+3 ; 1 cycle
	t1sn	f, z ; 1 cycle + 1 cycle for final skip
	goto	00001$ ; 2 cycles
00101$:
;	delay.h: 95: }
	ret
;	main.c: 28: void main() {
;	-----------------------------------------
;	 function main
;	-----------------------------------------
_main:
;	main.c: 31: PAC &= ~(1 << INPUT_PIN);         /* Set input as input (all pins are input by default) */
	set0.io	__pac, #5
;	main.c: 32: PADIER |= (1 << INPUT_PIN);       /* input as digital input */
	set1.io	__padier, #5
;	main.c: 33: PAPH |= (1 << INPUT_PIN);         /* Enable pull-up resistor on input */
	set1.io	__paph, #5
;	main.c: 34: PAC |= (1 << PWM_OUTPUT_PIN);     /* Set PWM_OUPUT_PIN as output (all pins are input by default) */
	set1.io	__pac, #4
;	main.c: 37: PWMG1CUBL = PWM_MAX << 5;         /* Set the PWM upper bound (lower 3 bits) */
	mov	a, #0xe0
	mov.io	__pwmg1cubl, a
;	main.c: 38: PWMG1CUBH = PWM_MAX >> 3;         /* (upper 5 bits) */
	mov	a, #0x1f
	mov.io	__pwmg1cubh, a
;	main.c: 39: PWMG1DTL = 0x00;                  /* Clear the PWM duty value */
	mov	a, #0x00
	mov.io	__pwmg1dtl, a
;	main.c: 40: PWMG1DTH = 0x00;
	mov	a, #0x00
	mov.io	__pwmg1dth, a
;	main.c: 41: PWMG1C = (uint8_t)(PWMG1C_ENABLE | PWMG1C_OUT_PA4 | PWMG1C_CLK_IHRC);
	mov	a, #0x87
	mov.io	__pwmg1c, a
;	main.c: 42: PWMG1S = 0x00;                    /* No pre-scaler */
	mov	a, #0x00
	mov.io	__pwmg1s, a
;	main.c: 46: while (1) {
00109$:
;	main.c: 48: if (isInputActive()) {
	mov.io	a, __pa
	and	a, #0x20
	ceqsn	a, #0x00
	goto	00106$
;	main.c: 51: for (pwmValue = PWM_MIN; pwmValue < PWM_MAX; pwmValue += PWM_INC_VALUE) {
	mov	a, #0x80
	mov	_main_sloc0_1_0+0, a
	clear	_main_sloc0_1_0+1
00111$:
;	main.c: 52: PWMG1DTL = pwmValue << 5;     /* Set PWM duty value (lower 3 bits) */
	mov	a, _main_sloc0_1_0+0
	swap	a
	and	a, #0xf0
	sl	a
	mov.io	__pwmg1dtl, a
;	main.c: 53: PWMG1DTH = pwmValue >> 3;     /* (upper 8 bits) */
	mov	a, _main_sloc0_1_0+1
	mov	p, a
	mov	a, _main_sloc0_1_0+0
	sr	p
	src	a
	sr	p
	src	a
	sr	p
	src	a
	mov.io	__pwmg1dth, a
;	main.c: 54: _delay_ms(PWM_RAMP_DELAY_ms);
	mov	a, #0xe6
	mov	__delay_loop_16_PARM_1+0, a
	mov	a, #0x03
	mov	__delay_loop_16_PARM_1+1, a
	call	__delay_loop_16
;	main.c: 51: for (pwmValue = PWM_MIN; pwmValue < PWM_MAX; pwmValue += PWM_INC_VALUE) {
	mov	a, _main_sloc0_1_0+0
	add	a, #0x04
	mov	p, a
	mov	a, _main_sloc0_1_0+1
	addc	a
	mov	_main_sloc0_1_0+1, a
	mov	a, p
	mov	_main_sloc0_1_0+0, a
	mov	a, _main_sloc0_1_0+1
	mov	p, a
	mov	a, _main_sloc0_1_0+0
	sub	a, #0xff
	mov	a, p
	subc	a
	t0sn.io	f, c
	goto	00111$
;	main.c: 58: PWMG1DTL = PWM_MAX << 5;     /* Set PWM duty value (lower 3 bits) */
	mov	a, #0xe0
	mov.io	__pwmg1dtl, a
;	main.c: 59: PWMG1DTH = PWM_MAX >> 3;     /* (upper 8 bits) */
	mov	a, #0x1f
	mov.io	__pwmg1dth, a
;	main.c: 60: while(isInputActive()) {
00102$:
	mov.io	a, __pa
	and	a, #0x20
	ceqsn	a, #0x00
	goto	00109$
;	main.c: 61: _delay_ms(1000);
	mov	a, #0x84
	mov	__delay_loop_32_PARM_1+0, a
	mov	a, #0x45
	mov	__delay_loop_32_PARM_1+1, a
	mov	a, #0x01
	mov	__delay_loop_32_PARM_1+2, a
	clear	__delay_loop_32_PARM_1+3
	call	__delay_loop_32
	goto	00102$
00106$:
;	main.c: 65: PWMG1DTL = 0;                 /* Set PWM duty value (lower 3 bits) */
	mov	a, #0x00
	mov.io	__pwmg1dtl, a
;	main.c: 66: PWMG1DTH = 0;                 /* (upper 8 bits) */
	mov	a, #0x00
	mov.io	__pwmg1dth, a
;	main.c: 67: _delay_ms(50);                /* short delay for debounce */
	mov	a, #0x68
	mov	__delay_loop_16_PARM_1+0, a
	mov	a, #0x18
	mov	__delay_loop_16_PARM_1+1, a
	call	__delay_loop_16
	goto	00109$
;	main.c: 70: }
	ret
;	main.c: 73: unsigned char _sdcc_external_startup(void) {
;	-----------------------------------------
;	 function _sdcc_external_startup
;	-----------------------------------------
__sdcc_external_startup:
;	main.c: 78: AUTO_INIT_SYSCLOCK();
	mov	a, #0x1c
	mov.io	__clkmd, a
;	main.c: 83: AUTO_CALIBRATE_SYSCLOCK(TARGET_VDD_MV);
	and	a, #'R'                       
	and	a, #'C'                       
	and	a, #(1)            
	and	a, #((1000000))     
	and	a, #((1000000)>>8)  
	and	a, #((1000000)>>16) 
	and	a, #((1000000)>>24) 
	and	a, #((5000))     
	and	a, #((5000)>>8)  
	and	a, #(0x0b)             
;	main.c: 85: return 0;   // Return 0 to inform SDCC to continue with normal initialization.
;	main.c: 86: }
	ret	#0x00
	.area CODE
	.area CONST
	.area CABS (ABS)

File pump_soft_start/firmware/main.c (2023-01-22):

/* Vacuum Pump Soft Start
 *  Use PWM to soft start a small DC vacuum pump to prevent current 
 *  surge that browns out the rest of the circuit.
 * 
 *  PA5 is an input from an opto that is triggered by the output of a 555 timer
 *  PA4 is an PWM output to a N-Channel Mosfet
 */

#include <stdint.h>
#include <pdk/device.h>
#include "auto_sysclock.h"
#include "delay.h"

#define INPUT_PIN             5     /* input pin is PA5 with an active low configuration */

// input is active low, so define helper for better readability below
#define isInputActive()       !(PA & (1 << INPUT_PIN))

#define PWM_MIN               128   /* PWM duty cycle will start at this value */
#define PWM_MAX               255   /* 11-bit PWM peripheral */
#define PWM_OUTPUT_PIN        4     /* PWM output pin is PA4/PG1PWM */

// Targeting a <1 second soft startup
#define PWM_RAMP_DELAY_ms     8     /* delay in call to increase PWM duty cycle */
#define PWM_INC_VALUE         4     /* value to increase PWM duty cycle by */

// Main program
void main() {

  // Initialize hardware
  PAC &= ~(1 << INPUT_PIN);         /* Set input as input (all pins are input by default) */
  PADIER |= (1 << INPUT_PIN);       /* input as digital input */
  PAPH |= (1 << INPUT_PIN);         /* Enable pull-up resistor on input */
  PAC |= (1 << PWM_OUTPUT_PIN);     /* Set PWM_OUPUT_PIN as output (all pins are input by default) */
  
  // Setup PWM peripheral
  PWMG1CUBL = PWM_MAX << 5;         /* Set the PWM upper bound (lower 3 bits) */
  PWMG1CUBH = PWM_MAX >> 3;         /* (upper 5 bits) */
  PWMG1DTL = 0x00;                  /* Clear the PWM duty value */
  PWMG1DTH = 0x00;
  PWMG1C = (uint8_t)(PWMG1C_ENABLE | PWMG1C_OUT_PA4 | PWMG1C_CLK_IHRC);
  PWMG1S = 0x00;                    /* No pre-scaler */
  // PWMG1S = (uint8_t)(PWMG1S_PRESCALE_DIV16 | PWMG1S_SCALE_DIV16);

  // Main processing loop
  while (1) {

    if (isInputActive()) {
      uint16_t pwmValue;
      // ramp up PWM output
      for (pwmValue = PWM_MIN; pwmValue < PWM_MAX; pwmValue += PWM_INC_VALUE) {
        PWMG1DTL = pwmValue << 5;     /* Set PWM duty value (lower 3 bits) */
        PWMG1DTH = pwmValue >> 3;     /* (upper 8 bits) */
        _delay_ms(PWM_RAMP_DELAY_ms);
      }

      // set PWM output to max, ie pin is fully high         
      PWMG1DTL = PWM_MAX << 5;     /* Set PWM duty value (lower 3 bits) */
      PWMG1DTH = PWM_MAX >> 3;     /* (upper 8 bits) */
      while(isInputActive()) {
        _delay_ms(1000);
      }
    } else {
      // set PWM output to min, ie pin is fully low
      PWMG1DTL = 0;                 /* Set PWM duty value (lower 3 bits) */
      PWMG1DTH = 0;                 /* (upper 8 bits) */
      _delay_ms(50);                /* short delay for debounce */
    }
  }
}

// Startup code - Setup/calibrate system clock
unsigned char _sdcc_external_startup(void) {

  // Initialize the system clock (CLKMD register) with the IHRC, ILRC, or EOSC clock source and correct divider.
  // The AUTO_INIT_SYSCLOCK() macro uses F_CPU (defined in the Makefile) to choose the IHRC or ILRC clock source and divider.
  // Alternatively, replace this with the more specific PDK_SET_SYSCLOCK(...) macro from pdk/sysclock.h
  AUTO_INIT_SYSCLOCK();

  // Insert placeholder code to tell EasyPdkProg to calibrate the IHRC or ILRC internal oscillator.
  // The AUTO_CALIBRATE_SYSCLOCK(...) macro uses F_CPU (defined in the Makefile) to choose the IHRC or ILRC oscillator.
  // Alternatively, replace this with the more specific EASY_PDK_CALIBRATE_IHRC(...) or EASY_PDK_CALIBRATE_ILRC(...) macro from easy-pdk/calibrate.h
  AUTO_CALIBRATE_SYSCLOCK(TARGET_VDD_MV);

  return 0;   // Return 0 to inform SDCC to continue with normal initialization.
}

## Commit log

2021-04-25 init commit
    [smd_vacuum.kicad_pcb, smd_vacuum.sch]
2021-04-25 board layout
    [smd_vacuum.kicad_pcb, smd_vacuum.sch]
2021-04-25 plot gerbers
    [smd_vacuum.kicad_pcb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]
2021-04-25 update spindle speed
2021-04-27 add polarity protection pmos part number
    [smd_vacuum.sch]
2021-04-27 add rc to 555 reset for power on reset
    [smd_vacuum.sch]
2021-04-27 layout pcb with reset circuitry
    [smd_vacuum.kicad_pcb, smd_vacuum.sch]
2021-05-16 add spacers
    [air_spacer.scad, air_spacer.stl, pump_spacer.scad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]
2021-06-06 output schematic
2021-06-06 create iBOM
    [smd_vacuum.kicad_pcb]
2022-05-03 ignore kicad backups
2022-05-03 to new kicad version
    [smd_vacuum.kicad_sch, smd_vacuum.sch]
2022-05-03 export updated pcb gerbers
    [smd_vacuum.kicad_pcb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]
2022-05-03 move origin
    [smd_vacuum.kicad_pcb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]
2022-05-03 updated gcode
    [smd_vacuum_0.8mm.drl, smd_vacuum_1.1mm.drl, smd_vacuum_3.2mm.drl]
2022-06-27 create file
    [KarlssonRobotics_pump_mount-base.amf, KarlssonRobotics_pump_mount-clamp.amf, KarlssonRobotics_pump_mount.FCStd]
2023-01-21 create soft start circuit
    [soft_pump_start.kicad_pcb, soft_pump_start.kicad_sch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]
2023-01-22 PWM timing fixes for acceptable startup lag
    [main.asm, main.c]
